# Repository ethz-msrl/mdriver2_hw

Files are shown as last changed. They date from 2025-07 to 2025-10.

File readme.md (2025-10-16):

# MDriver2 Hardware
This repository contains the hardware design files of the `MDriver2` project.
## Control Hardware
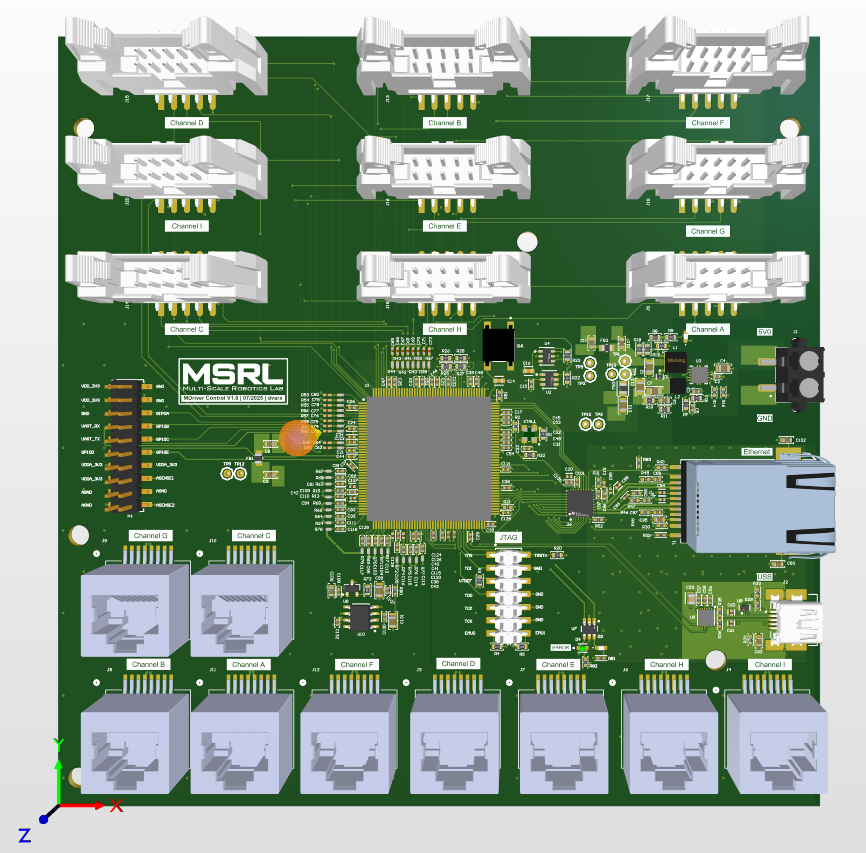
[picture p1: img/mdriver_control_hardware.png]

## Power Hardware
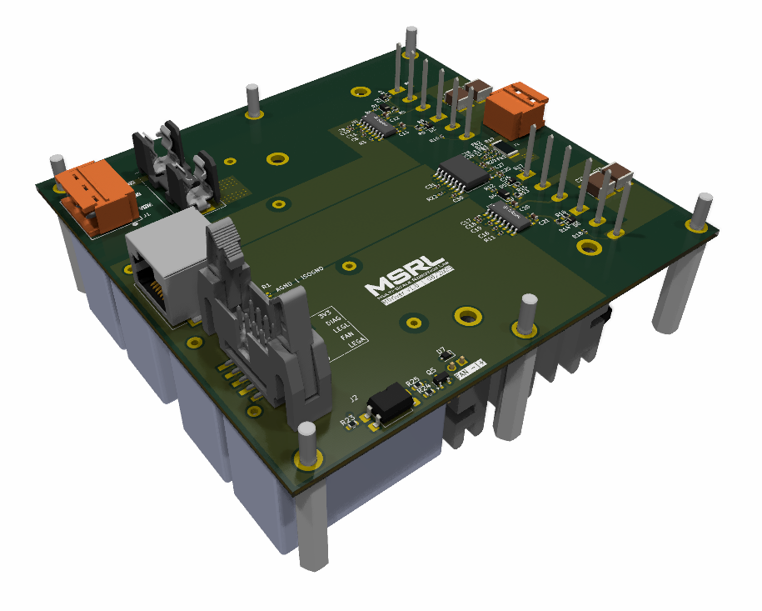
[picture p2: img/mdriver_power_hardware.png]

## Experimental Setup Overview
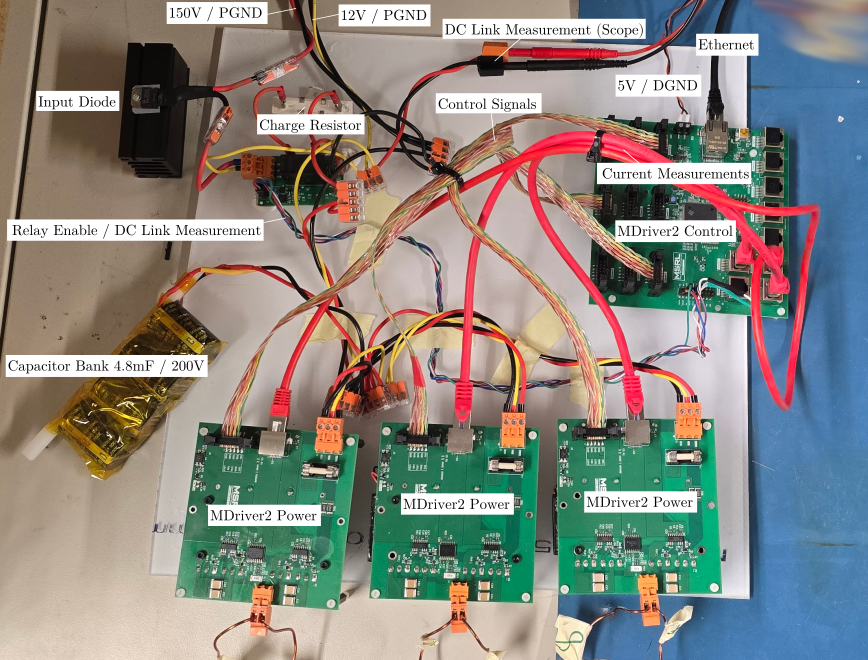
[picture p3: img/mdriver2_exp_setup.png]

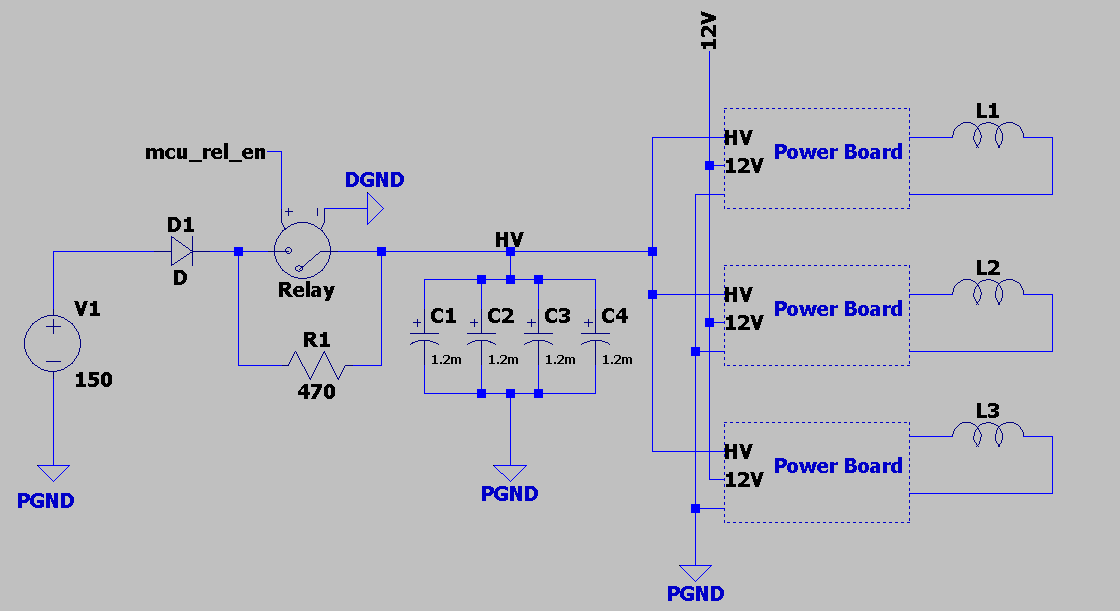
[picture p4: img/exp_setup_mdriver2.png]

- The input diode `D1` is optional and used to protect the supply `V1`.
- The charge resistor `R1` is used to limit excessive inrush current to the capcacitor bank but may not be needed for all supplies.
- The DC link voltage `VH` is monitored using an isolated DC measurement from the `capbank` PCB. Voltage values are transmitted via delta-sigma modulation to the microcontroller.

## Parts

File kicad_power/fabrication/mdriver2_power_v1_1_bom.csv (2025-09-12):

Reference | Qty | Partno | Description | Footprint
C6,C8,C11,C16,C19,C26,C27,C29,C30,C31,C32,C33 | 12 | C0402C104K4RECAUTO | Multilayer Ceramic Capacitors MLCC - SMD/SMT 16V 0.1uF X7R 0402 10% | Capacitor_SMD:C_0402_1005Metric
C7,C12,C13,C20,C21,C34 | 6 | CGA3E1X7S1C225K080AE | Cap Ceramic 2.2uF 16V X7S 10% Pad SMD 0603 Soft Termination 125C Automotive T/R | Capacitor_SMD:C_0603_1608Metric
C9,C10,C17,C18 | 4 | VJ0402A101JXACW1BC | 0402 100 pF 50 V ±5% Tolerance C0G/NP0 SMT Multilayer Ceramic Chip Capacitor | Capacitor_SMD:C_0402_1005Metric
C14,C15,C22,C23 | 4 | 885342214001 | Cap, 1Uf, 630V, Mlcc, 2220 Rohs Compliant: Yes |Wurth Elektronik 885342214001 | Capacitor_SMD:C_2220_5750Metric_Pad1.97x5.40mm_HandSolder
C24,C25 | 2 | 0402YD105KAT2A | Multilayer Ceramic Capacitor, 1uF, 10%, X5R, 16 V, 0402 [1005 Metric] Rohs Compliant: Yes | Capacitor_SMD:C_0402_1005Metric
C28 | 1 | CL05B102KB5NNNC | 1000 pF ±10% 50V Ceramic Capacitor X7R 0402 (1005 Metric) | Capacitor_SMD:C_0402_1005Metric
D1,D4 | 2 | ES1JFL | ES1JFL Series 600 V 1 A Surface Mount Ultrafast Rectifier - SOD-123F | Diode_SMD:D_SOD-123F
D2,D3,D5,D6,D7 | 5 | SD107WS-7-F | SD107WS Series 30 V 750 mA Schottky Barrier Diode Surface Mount - SOD-323 | Diode_SMD:D_SOD-323F
F1 | 1 | 0031.8225 | Fuse Block 10 A 500V 1 Circuit Cartridge Surface Mount | mdriver:fuse
FB1,FB2,FB3 | 3 | 74269244182 | Ferrite Beads, 0.21A, 1.8Kohm, 25% Rohs Compliant: Yes |Wurth Elektronik 74269244182 | Inductor_SMD:L_0402_1005Metric
J2 | 1 | 3010-10-003-13-00 | Generic connector, double row, 02x05, odd/even pin numbering scheme (row 1 odd numbers, row 2 even numbers), script generated (kicad-library-utils/schlib/autogen/connector/) | mdriver:10pin_data_connector
J3 | 1 | 634008149821 | Modular Jack WR-MJ, Tab Up, Shielded, Horizontal Entry, SMT, 8P8C | mdriver:J_Wurth_WR-MJ_634008149821
Q5 | 1 | Nexperia BC817-25,235 | Single Bipolar Transistor, NPN, 45 V, 500 mA, 345 mW, SOT-23 (TO-236AB), 3 Pins, Surface Mount | Package_TO_SOT_SMD:SOT-23
R2 | 1 | CRCW04021M00FKED | 63mW Thick Film Resistors 75V ±1% ±100ppm/℃ 1MΩ 0402 Chip Resistor - Surface Mount ROHS | Resistor_SMD:R_0402_1005Metric
R3,R11 | 2 | RCA04020000ZSED | Zero Ohm Resistor, Jumper, 0402 [1005 Metric], Thick Film, 63 mW, 1.5 A, Surface Mount Device | Resistor_SMD:R_0402_1005Metric
R4,R12 | 2 | CRGP1206F18R | Res Thick Film 1206 18 Ohm 1% 0.5W(1/2W) ±100ppm/C Pad SMD Automotive T/R | Resistor_SMD:R_1206_3216Metric
R5,R6,R13,R14 | 4 | CRCW06030000ZSTB | Zero Ohm Resistor, Jumper, 0603 [1608Metric], Thick Film, 100 mW, 2 A, Surface Mount | Resistor_SMD:R_0603_1608Metric
R7,R8,R15,R16 | 4 | ERJPA3F12R0V | Res Thick Film 0603 12 Ohm 1% 0.25W(1/4W) ±100ppm/C Pad SMD T/R Automotive AEC-Q200 | Resistor_SMD:R_0603_1608Metric
R9,R10,R17,R18 | 4 | CRGCQ0402F560K | Res Thick Film 0402 560K Ohm 1% 0.063W(1/16W) ±100ppm/C Pad SMD Automotive T/R | Resistor_SMD:R_0402_1005Metric
R19 | 1 | MCS3264R005FER | Fixed Resistor, 2W, 0.005ohm, 0.1V, 1% +/-Tol, 100ppm/Cel, Surface Mount, 2512 | Resistor_SMD:R_2512_6332Metric_Pad1.40x3.35mm_HandSolder
R20,R21 | 2 | RC0402JR-0710RL | Res Thick Film 0402 10 Ohm 5% 0.063W(1/16W) ±200ppm/C Pad SMD T/R | Resistor_SMD:R_0402_1005Metric
R22 | 1 | CRGP0402F47K | TE Connectivity CRGP0402F47K Res Thick Film 0402 47K Ohm 1% 0.125W(1/8W) ±100ppm/°C Pad SMD T/R Automotive AEC-Q200 | Resistor_SMD:R_0402_1005Metric
R23,R24,R25 | 3 | ERJ-PA3F4300V | Res Thick Film 0603 430 Ohm 1% 0.25W(1/4W) ±100ppm/C Pad SMD T/R Automotive AEC-Q200 | Resistor_SMD:R_0603_1608Metric
R26,R27 | 2 | 4-2176331-7 | Fixed Resistor, Thick Film, 2W, 68000ohm, 500V, 1% +/-Tol, 100ppm/Cel, Surface Mount, 2512 | Resistor_SMD:R_2512_6332Metric
U1,U2 | 2 | 2EDB8259YXUMA1 | Fast, robust, dual-channel, functional isolated MOSFET gate drivers with accurate and stable timing. | mdriver:SOIC-16
U3 | 1 | AMC3302DWER | ±50-mV input, precision current sensing reinforced isolated amplifier with integrated DC/DC | mdriver:AMC3302DWER
U4 | 1 | SFH617A-1X007T | Optocoupler, Phototransistor Output, 5300 VRMS, VCEO 70V, CTR% 40-80, -55 to +110 degree Celsius, UL, BSI, FIMKO, cUL, 8mm clearence SMD PDIP-4 | Package_DIP:SMDIP-4_W9.53mm_Clearance8mm

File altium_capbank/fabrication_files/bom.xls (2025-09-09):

Comment | Designator | Footprint | JLCPCB
C0603 15,000 pF C0G 30ppm/°C 20.00% 25 V | C1, C4 | FP-C0603C-CF-MFG | C1596
MLCC 1uF 0603 | C3, C5, C6 | CAPC1608X87X35LL15T15 | C5673
Single Output LDO, 100 mA, Fixed 5 V Output, 5.38 to 16 V Input, with Low IQ, 5-pin SOT-23 (DBV), -40 to 125 degC, Green (RoHS & no Sb/Br) | U2 | DBV0005A_M | C9837
Schottky Barrier Diode, 2-Pin SOD-323, Pb-Free, Tape and Reel | D1 | ONSC-SOD-323-2-477-02_V | C21107
Resistor | R3 | RES 0805_2012 | C17444
SMT Resistor | R4, R5, R6, R8, R9, R10, R11, R7 | RES 0603_1608 | C22961
SMT Resistor | R2 | RES 0603_1608 | C23193
Chip Multilayer Ceramic Capacitors for General Purpose, 0603, 2.2uF, X7R, 15%, 10%, 10V | C2 | FP-GRM188-0_1-e0_2_0_5-MFG | C43922
MOSFET N-CH 60V 1.6A SOT23 | Q1 | FP-SOT23-MFG | C211403
Optocoupler Phototransistor Output, 6 V, 50 mA, -55 to 100 degC, 4-Pin SOIC, RoHS, Tape and Reel | U1 | VISH-SOP-4_A_V | C335248
&plusmn;1-V input, precision voltage sensing reinforced isolated modulator 8-SOIC -40 to 125 | U3 | AMC1336 | C1852019
CONN HEADER SMD 6POS 2.54mm | J2 | FP-TMM-103-01-G-D-SM-MFG | C192301

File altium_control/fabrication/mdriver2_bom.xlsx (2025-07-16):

Designator | Quantity | Description | Manufacturer Partno
C1, C4, C7, C99, C131 | 5 | MLCC 22uF 0805 5V | GRM21BR60J226ME39L
C2, C3, C5, C15, C17, C21, C22, C23, C24, C25, C26, C29, C30, C31, C32, C33, C34, C36, C37, C38, C39, C40, C41, C42, C43, C44, C45, C46, C47, C48, C49, C52, C53, C54, C56, C57, C58, C81, C82, C87, C88, C89, C90, C91, C92, C93, C94, C95, C96, C100, C103, C104, C105, C107, C108, C109, C110, C111, C112, C113, C114, C115, C116, C117, C118, C119, C120, C121, C122, C123, C124, C125, C130, C132 | 80 | MLCC 100nF 0402 10V | C0402C104K8PACTU
C6 | 1 | MLCC 33pF 0603 10V C0G | 06035A330JAT2A
C8, C9, C10, C11, C106 | 5 | MLCC 2.2uF 0603 10V | GRM188R71A225KE15D
C12, C13 | 2 | MLCC 10uF 0805 10V | C0805C106K8PACTU
C14, C16 | 2 | CAP CER 10000PF 50V X7R 0603 | CC0603KRX7R9BB103
C19, C98 | 2 | CAP CER 10UF 10V X5R 0402 | CL05A106MP5NUNC
C20, C55, C84, C86, C126, C127, C128, C129 | 8 | CAP CER 1UF 10V X5R 0402 | C0402C105K8PACTU
C59 | 1 | CAP CER 4.7UF 10V X5R 0805 | C0805C475K8PACTU
C60, C61 | 2 | CAP CER 47PF 50V C0G/NP0 0402 | C0402C470J5GACTU
C62, C83, C85, C102 | 4 | MLCC 4.7nF 0603 10V | C0603C472J5RACTU
C63, C64, C65, C66, C67, C68, C69, C70, C71, C72, C73, C74, C75, C76, C77, C78, C79, C80 | 18 | MLCC 0402 100pF | GRM1555C1H101JA01D
C97, C101 | 2 | MLCC 10nF 0402 5V | CC0402KRX7R7BB103
D1 | 1 | CFSH05-20L TR PBFREE Rectifier Diode, Schottky, 1 Phase, 1 Element, 0.1A, 30V V(RRM) | CFSH05-20L TR PBFREE
D2, D3 | 2 | 150060GS55040 WL-SMCD SMT Mono-color Chip LED Diffused | 150060GS55040
D4 | 1 | LED RED 0603 SMD | VLMS1300-GS08
FB1, FB2 | 2 | 60 Ohms @ 100 MHz 1 Power, Signal Line Ferrite Bead 0805 (2012 Metric) 5A 20mOhm | MH2029-600Y
FB3 | 1 | Chip Ferrite Bead, 0805, 220Ω @ 100MHz, 0.045Ω, 25%, 2A | BLM21PG221SN1D
J1 | 1 | SMD Terminal Block 6A | 691709710302
J2 | 1 | USB Connector, 30 V, 1 A, 0 to 50 degC, 5-Pin SMD, RoHS, Tape and Reel | 56579-0576
J3, J4, J6, J7, J8, J9, J10, J11, J12 | 9 | No Description Available | 1433900000
J5, J13, J14, J15, J16, J17, J18, J19, J20 | 9 | Pin header male 2x5 2.54mm | 3010-10-003-13-00
L1 | 1 | WE-LQS SMD Power Inductor, L=2.2 µH | 74404042022
L2 | 1 | WE-LQS SMD Power Inductor, L=3.3 µH | 74404032033
P1 | 1 | 0.025" SQ Post Header, Surface Mount, Vertical, -55 to 125 degC, 2.54 mm Pitch, 14-Pin, Male, RoHS | TSM-107-01-L-DV
P4 | 1 | Pin header SMD 10x2 | 61032021121
R1, R6, R7, R73 | 4 | Resistor 0Ohm 0603 | RC0603JR-070RL
R2 | 1 | Resistor 10Ohm 0402 | ERJ-2RKF10R0X
R3 | 1 | Resistor 100Ohm 0402 | ERJ-2RKF1000X
R4, R5, R29 | 3 | Resistor 4.7kOhm 0402 | ERJ-2RKF4701X
R8 | 1 | Resistor 340kOhm 0603 | CPF0603B340KE1
R9 | 1 | Resistor 680Ohm 0603 | ERJ-3EKF6800V
R10 | 1 | Resistor 22kOhm 0603 | RC0603FR-0722KL
R11 | 1 | Resistor 205kOhm 0603 | CRCW0603205KFKEA
R12 | 1 | Resistor 2kOhm 0603 | ERJ-3EKF2001V
R13, R15, R17, R24, R63, R64, R65, R66, R67, R68, R69, R70, R71, R72, R74, R75, R76, R77, R78, R79 | 20 | Resistor 150Ohm 0402 | RC0402FR-07150RL
R14, R21, R33, R52 | 4 | Resistor 10kOhm 0402 | CRCW040210K0FKEDHP
R16 | 1 | Resistor 100kOhm 0402 | ERJ-2RKF1003X
R18 | 1 | Resistor 200kOhm 0603 | CRCW0603200KFKEA
R19 | 1 | Resistor 75kOhm 0603 | CRCW060375K0FKEA
R20, R22, R23, R25, R26, R32 | 6 | Resistor 2.2kOhm 0603 | RC0603FR-072K2L
R27, R28 | 2 | Resistor 56kOhm 0603 | CRCW060356K0FKEA
R30 | 1 | Resistor 2.49kOhm 0402 1% | CRCW04022K49FKED
R31 | 1 | Resistor 4.87kOhm 0402 1% | CRCW04024K87FKED
R34 | 1 | Resistor 1MOhm 0402 | CRGCQ0402F1M0
R35, R36 | 2 | Resistor 27Ohm 0402 | RC0402FR-0727RL
R37, R38, R39, R40, R41, R42, R43, R44, R45, R50, R53, R54, R55, R56, R57, R58, R61, R62 | 18 | Resistor 5.6Ohm 0402 | RC0402FR-075R6L
R46, R47, R48, R49 | 4 | Resistor 49.9Ohm 0402 | ERJ-2RKF49R9X
R51, R83 | 2 | Resistor 2.2kOhm 0402 | RC0402JR-072K2L
R59, R60 | 2 | Resistor 470Ohm 0603 | RC0603FR-07470RL
R80 | 1 | Resistor 2.2kOhm 0402 | BLM15AG102SN1D
R81, R82 | 2 | Resistor 1kOhm 0402 1% | CRCW04021K00FKED
SW1 | 1 | SWITCH TACTILE SPST-NO 0.05A 12V | PTS645SM43SMTR92LFS
T1 | 1 | 7498010210A Telecom and Datacom Connector, 8 Contact(s), Female, Right Angle, Surface Mount Terminal | 7498010210A
U1 | 1 | XF28388DPTPS | F28388DPTPS
U2 | 1 | IC SUPERVISOR 1 CHANNEL TSOT23-6 | TPS3702CX33DDCT
U3 | 1 | Buck Adjustable Regulator with 2.5 to 6 V Input and 0.6 to 6 V Output, -40 to 85 degC, 10-Pin SON (DRC), Green (RoHS & no Sb/Br) | TPS62420DRCR
U4 | 1 | IC SUPERVISOR 1 CHANNEL TSOT23-6 | TPS3702CX12DDCT
U5 | 1 | IC USB SERIAL BASIC UART 12DFN | FT234XD-R
U6 | 1 | IC INTERFACE SPECIALIZED 32VQFN | DP83822IRHBR
U7 | 1 | Dual Buffer/Driver with Open-Drain Output, DBV0006A, LARGE T&R | SN74LVC2G07DBVR
U8 | 1 | 20 ppm / degC Max, 100 uA Series Voltage Reference, -40 to 125 degC, 3-pin SOT-23 (DBZ), Green (RoHS & no Sb/Br) | REF3130AIDBZR
U9 | 1 | TVS DIODE 5.5V 6SON | TPD4S012DRYR
U10 | 1 | High-Speed, Single-Supply, Rail-to-Rail Operational Amplifier MicroAmplifier(TM) Series, 2.7 to 5.5 V, -40 to 85 degC, 8-pin SOIC (D8), Green (RoHS & no Sb/Br) | OPA350UA/2K5
XTAL1 | 1 | 25MHz Oscillator | ECS-2520S33-250-FN-TR

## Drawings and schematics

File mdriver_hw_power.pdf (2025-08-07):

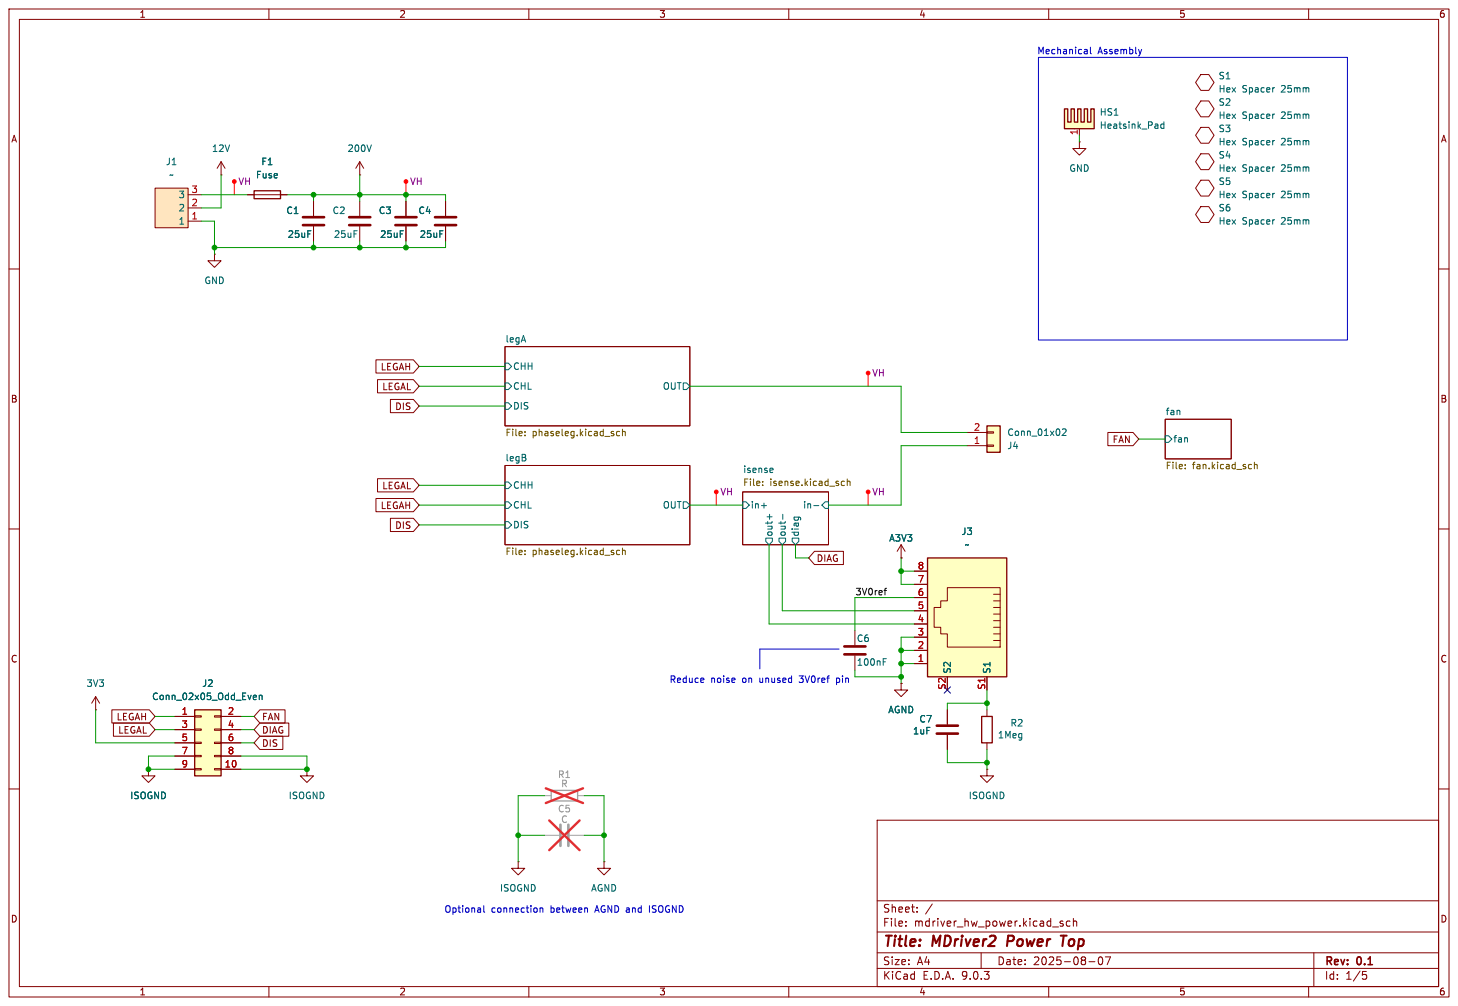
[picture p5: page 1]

fan File: fan.kicad_sch S6Hex Spacer 25mm

legB
isense File: isense.kicad_sch OUT CHH

File: mdriver_hw_power.kicad_sch Sheet: /
Id: 1/5 Title: MDriver2 Power Top

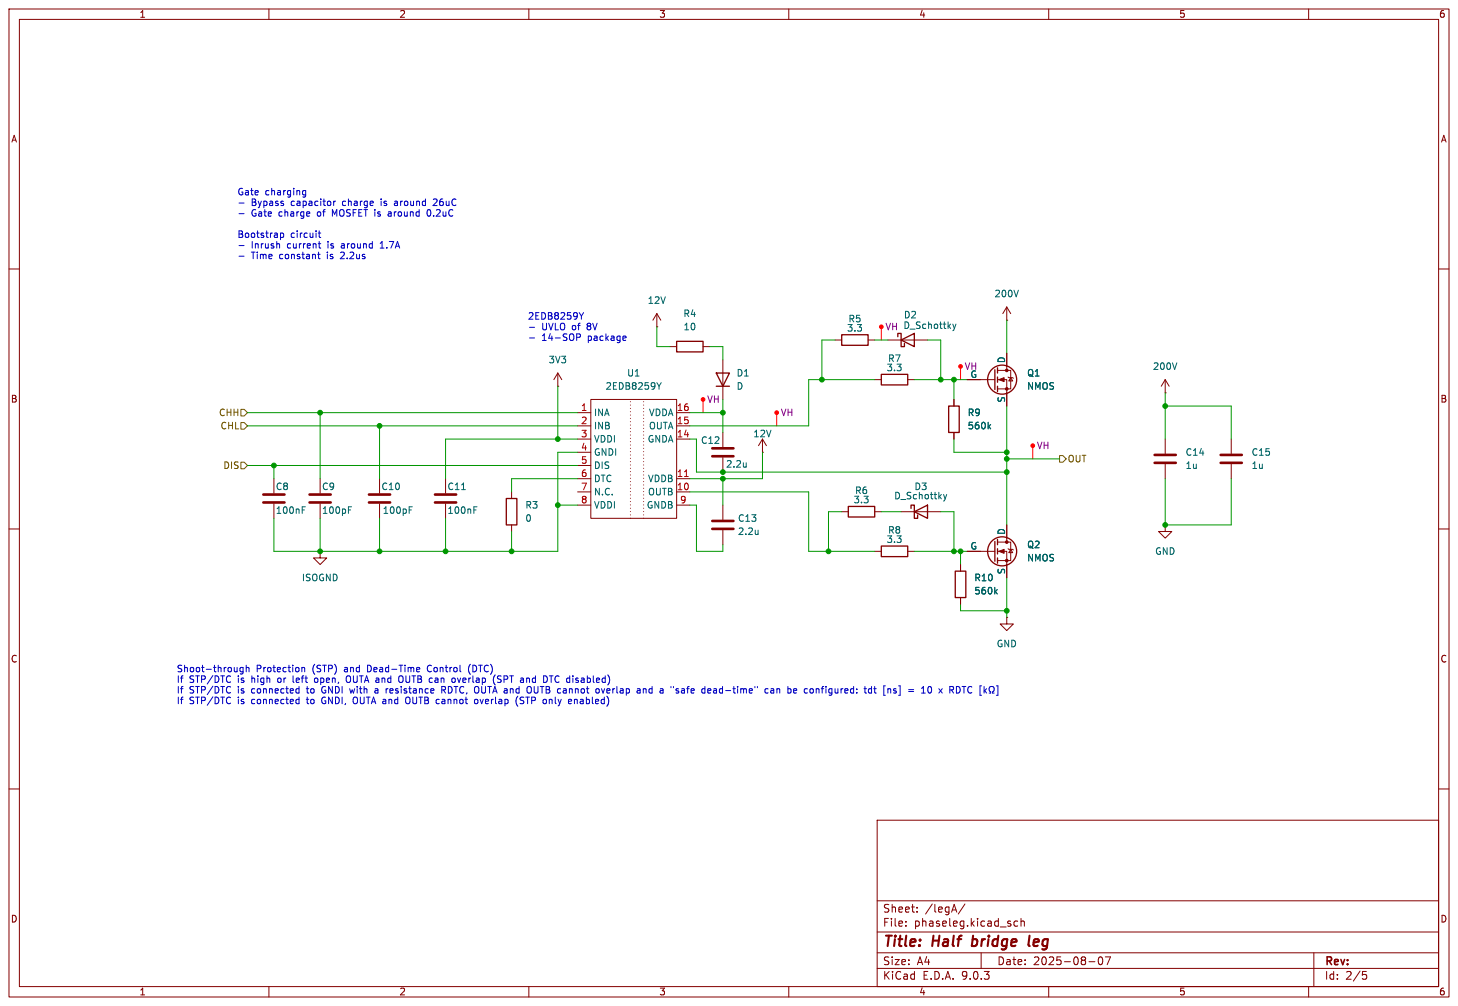
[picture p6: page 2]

- Gate charge of MOSFET is around 0.2uC

INB 2 VDDI 3 GNDI 4 DIS 5 DTC 6 N.C. 7 VDDI 8 INA 1 | VDDA 16 OUTA 15 GNDA 14 VDDB | 11 OUTB 10 GNDB 9 U1

If STP/DTC is high or left open, OUTA and OUTB can overlap (SPT and DTC disabled)

File: phaseleg.kicad_sch Sheet: /legA/
Id: 2/5 Title: Half bridge leg

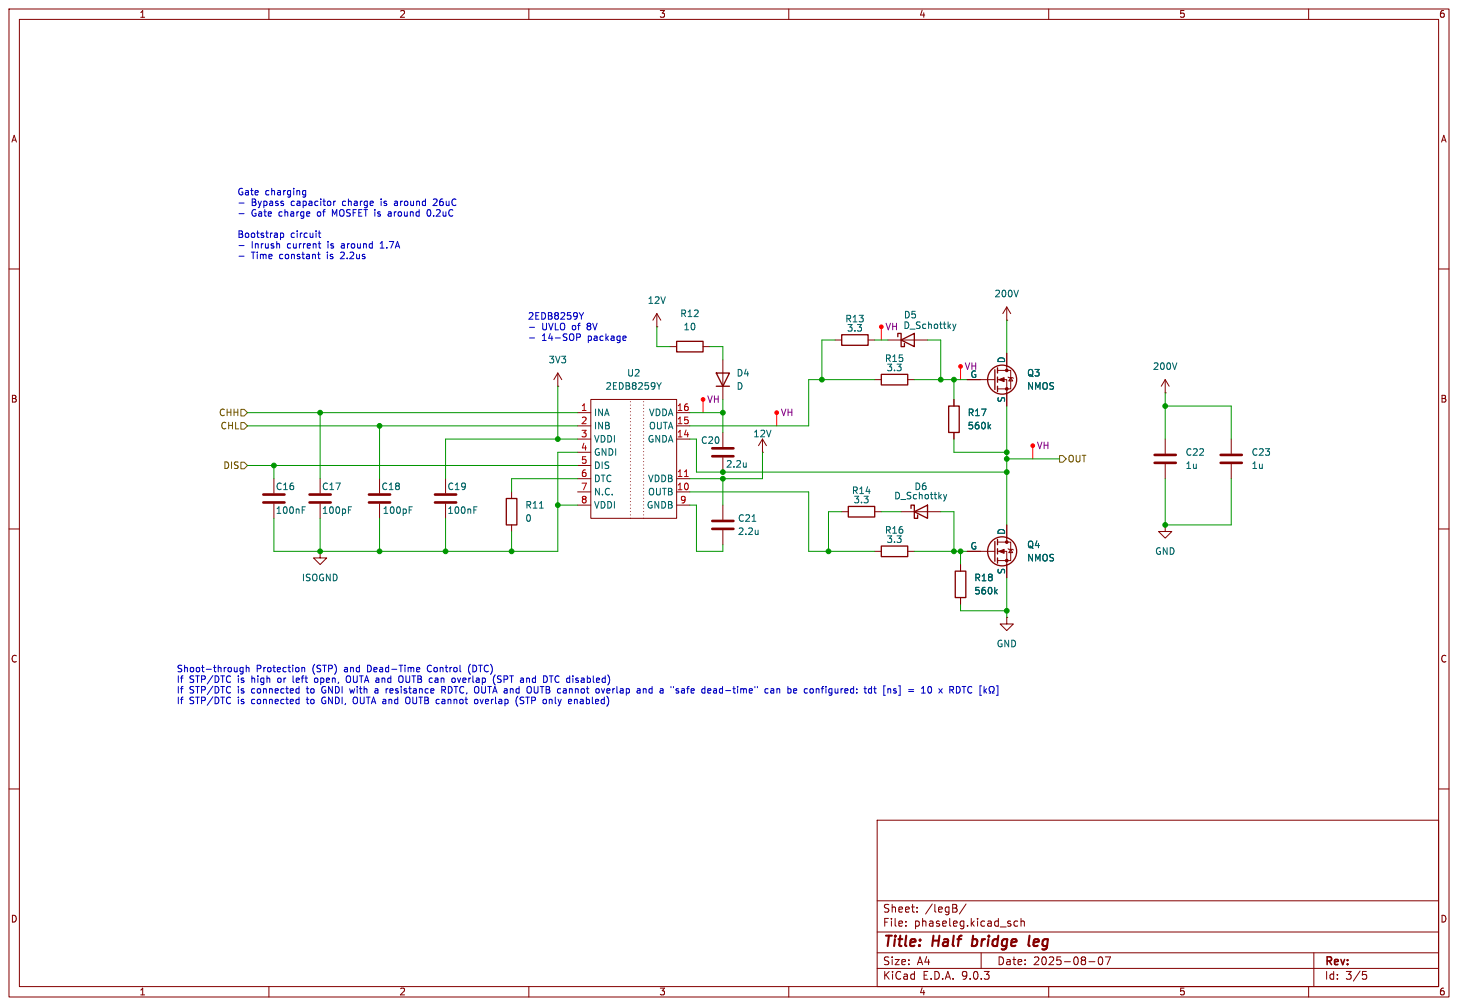
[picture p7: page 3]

- Gate charge of MOSFET is around 0.2uC

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

File: phaseleg.kicad_sch Sheet: /legB/
Id: 3/5 Title: Half bridge leg

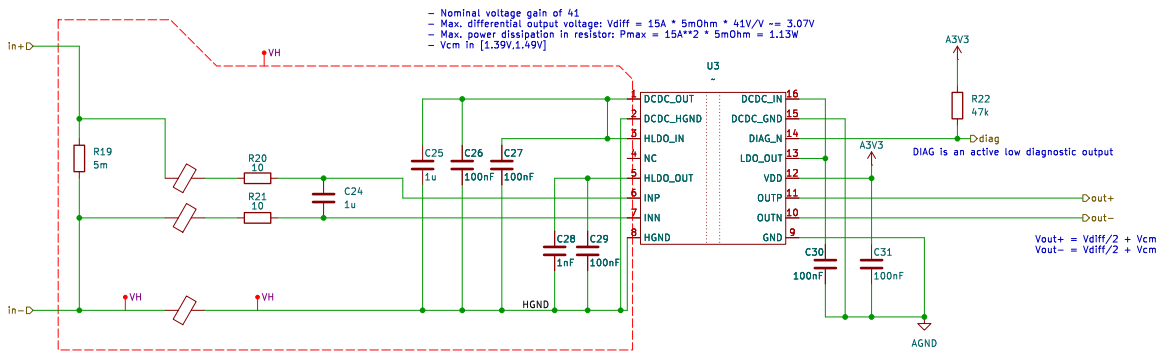
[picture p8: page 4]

- Nominal voltage gain of 41

File: isense.kicad_sch Sheet: /isense/
Id: 4/5 Title: Current sensing

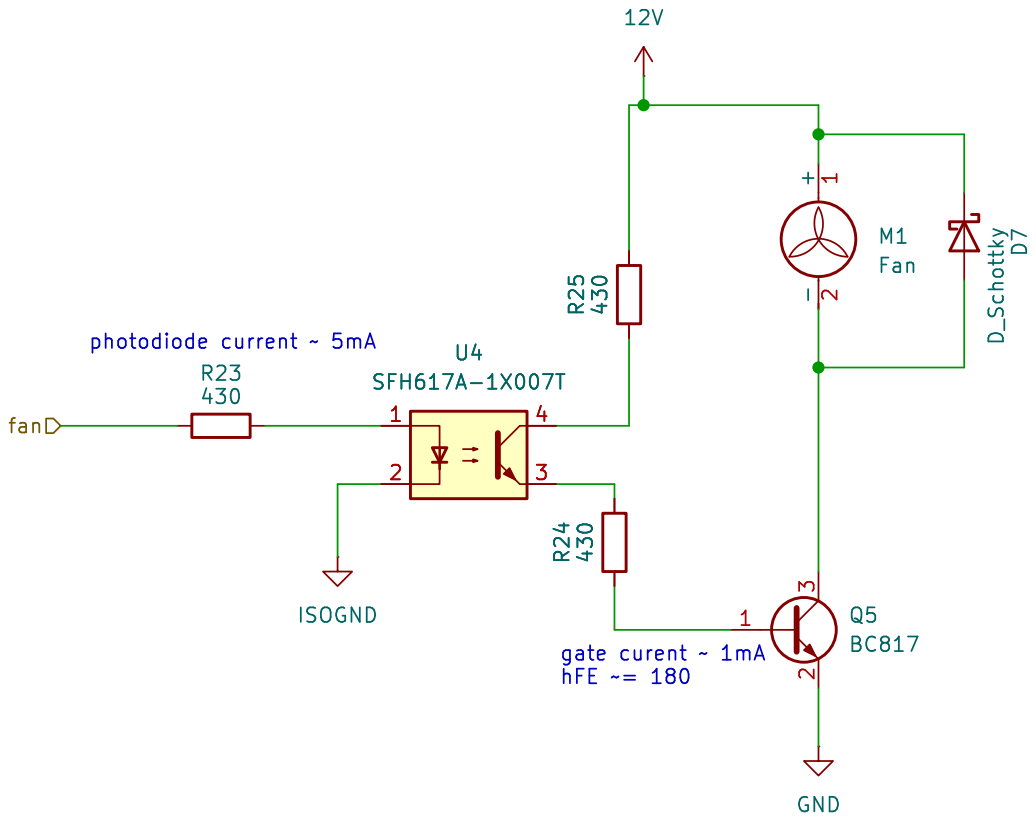
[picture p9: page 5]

Id: 5/5 Title: Cooling Fan Control File: fan.kicad_sch Sheet: /fan/ 1

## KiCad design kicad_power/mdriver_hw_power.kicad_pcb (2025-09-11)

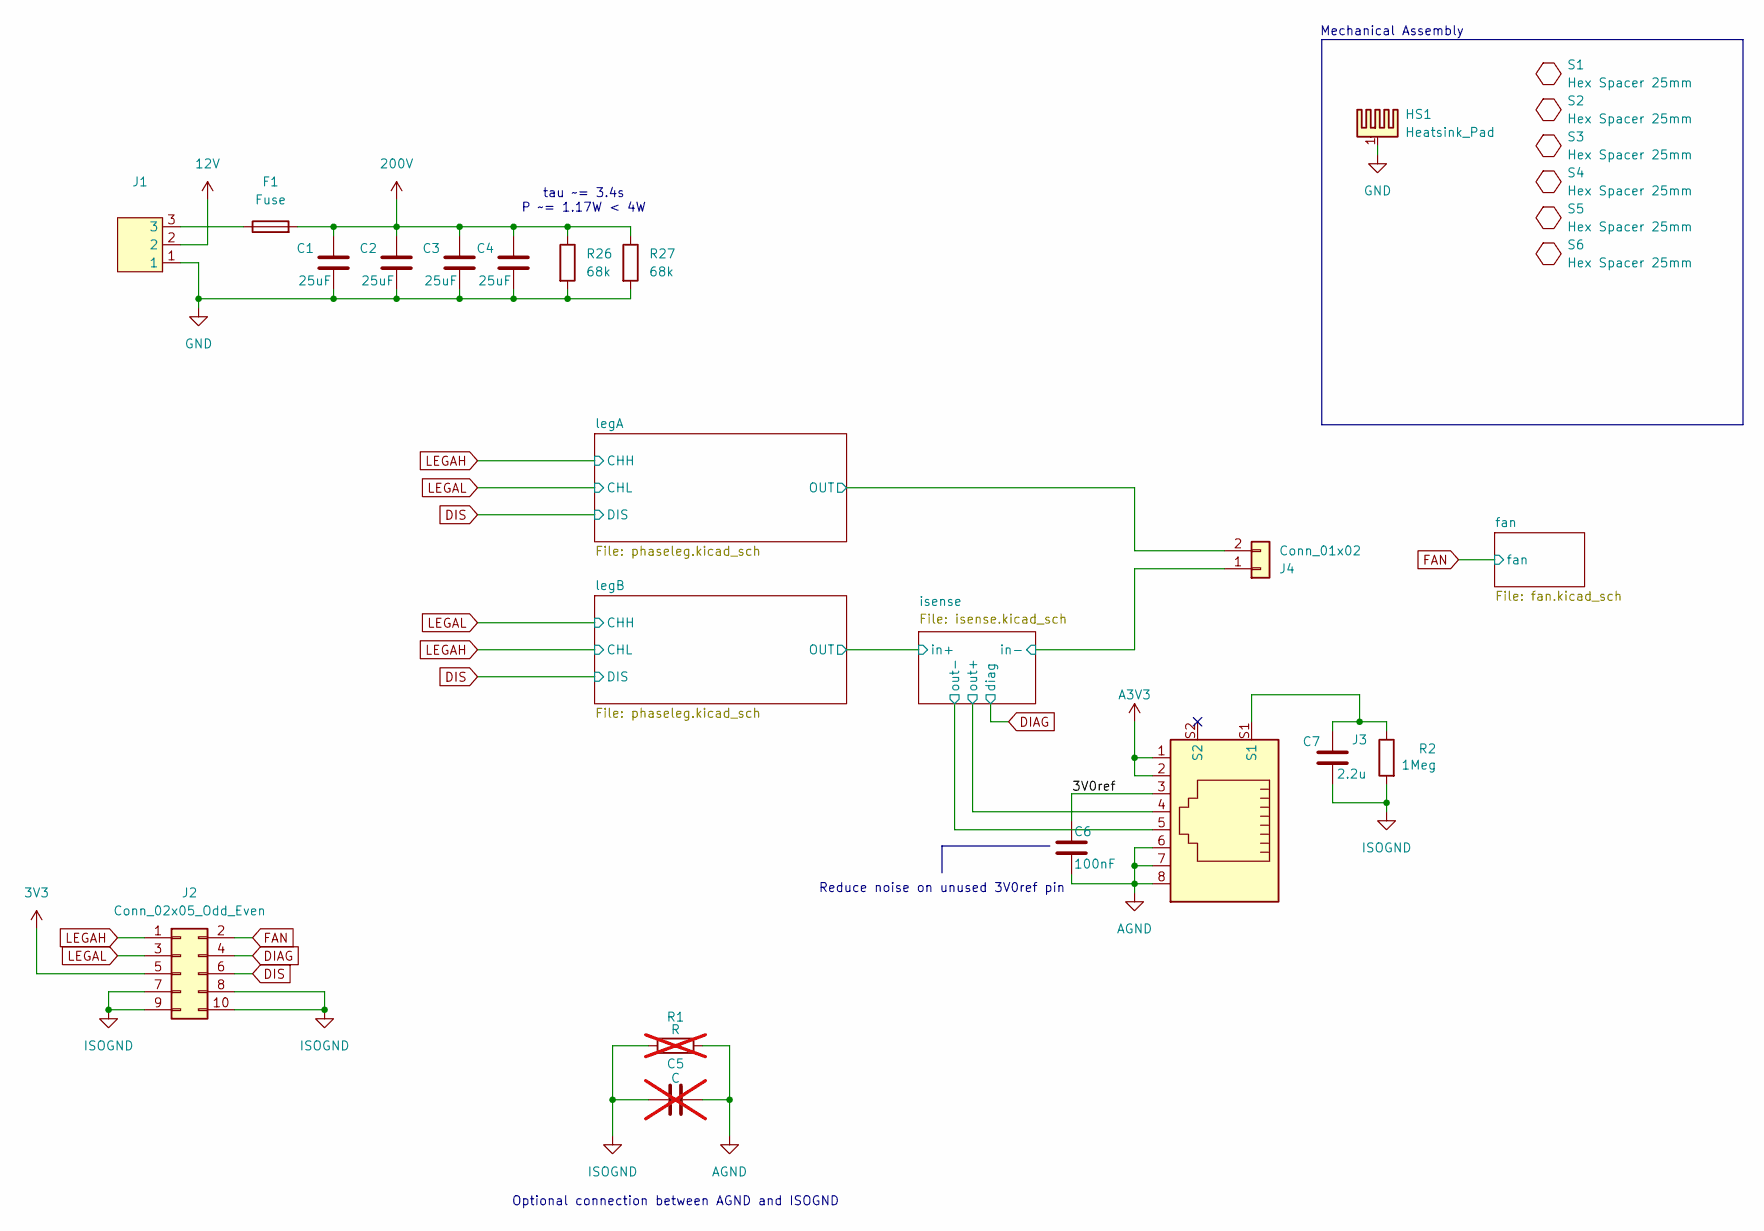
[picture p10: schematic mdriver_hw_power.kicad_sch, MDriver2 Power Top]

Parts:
C1, C2, C3, C4: 25uF; film_cap_25uF; Partno FB37F38I0256KC
C5: C; C_0402_1005Metric; not fitted
C6: 100nF; C_0402_1005Metric; Partno C0402C104K4RECAUTO; JLCPCB C1525
C7: 2.2u; C_0603_1608Metric; Partno CGA3E1X7S1C225K080AE; JLCPCB CL10A225KA8NNNC
F1: Fuse; fuse; Partno 0031.8225
HS1: Heatsink_Pad; heatsink_assman; Partno V5583K
J1: CONN_1148070000_WED; Partno 1148070000
J2: Conn_02x05_Odd_Even; 10pin_data_connector; Partno 3010-10-003-13-00
J3: J_Wurth_WR-MJ_634008149821; Partno 634008149821
J4: Conn_01x02; weidmuller_20A_2pin; Partno 1148030000
R1: R; R_0402_1005Metric; not fitted
R2: 1Meg; R_0402_1005Metric; Partno CRCW04021M00FKED; JLCPCB C26083
R26, R27: 68k; R_2512_6332Metric; Partno 4-2176331-7
S1, S2, S3, S4, S5, S6: Hex Spacer 25mm; hex_spacer; Partno 25506

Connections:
3V3: J2.5; also elsewhere on the board
12V: J1.2; also elsewhere on the board
200V: C1.1, C2.1, C3.1, C4.1, F1.2, R26.1, R27.1; also elsewhere on the board
/3V0ref: C6.1, J3.3
/isense/in-: J4.1; also elsewhere on the board
/isense/out+: J3.4; also elsewhere on the board
/isense/out-: J3.5; also elsewhere on the board
/legA/OUT: J4.2; also elsewhere on the board
A3V3: J3.1, J3.2; also elsewhere on the board
AGND: C5.2, C6.2, J3.6, J3.7, J3.8, R1.2; also elsewhere on the board
DIAG: J2.4; also elsewhere on the board
DIS: J2.6; also elsewhere on the board
FAN: J2.2; also elsewhere on the board
GND: C1.2, C2.2, C3.2, C4.2, HS1.1, J1.1, R26.2, R27.2; also elsewhere on the board
ISOGND: C5.1, C7.2, J2.7, J2.8, J2.9, J2.10, R1.1, R2.2; also elsewhere on the board
LEGAH: J2.1; also elsewhere on the board
LEGAL: J2.3; also elsewhere on the board
unnamed: C7.1, J3.S1, R2.1
unnamed: F1.1, J1.3

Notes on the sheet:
Optional connection between AGND and ISOGND
tau ~= 3.4s P ~= 1.17W < 4W
Mechanical Assembly
Reduce noise on unused 3V0ref pin

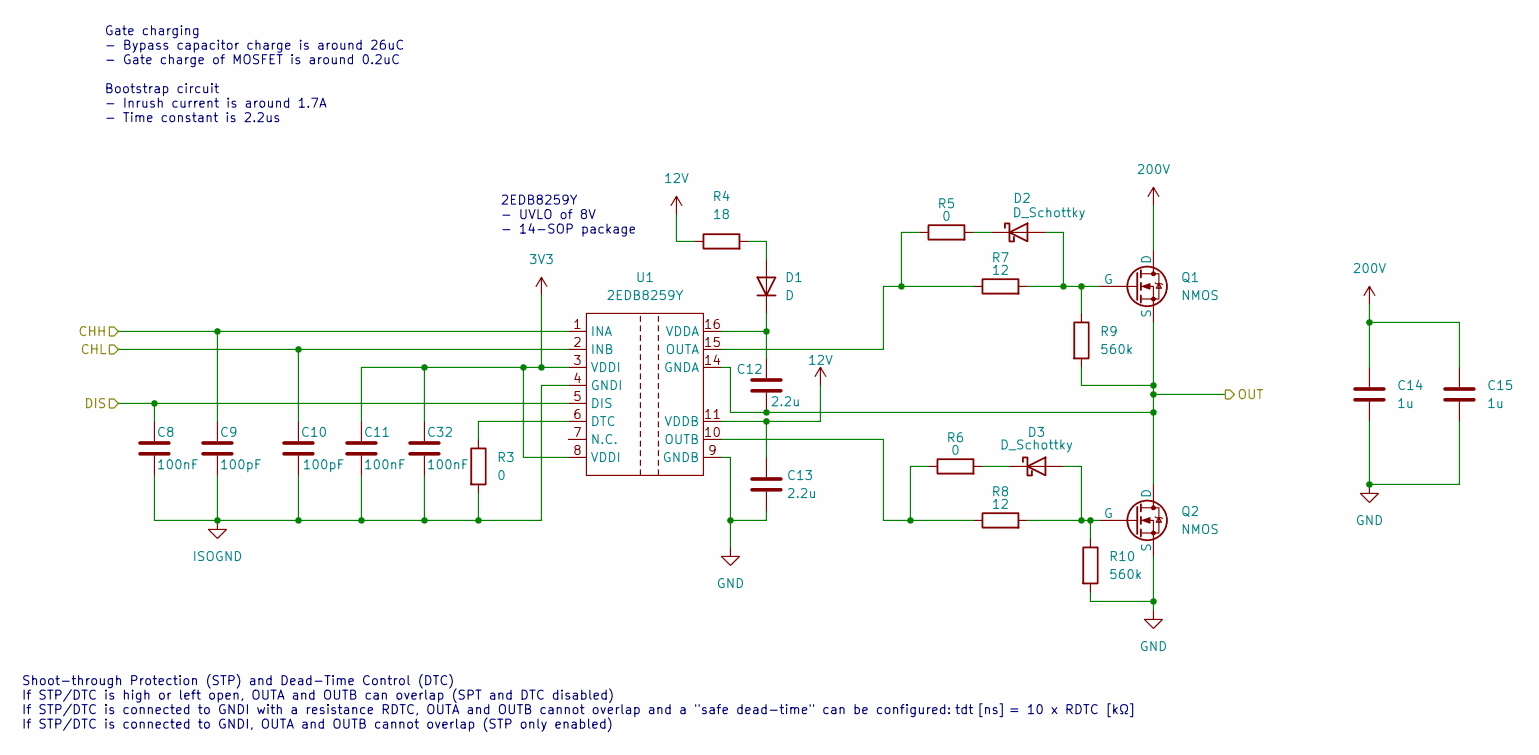
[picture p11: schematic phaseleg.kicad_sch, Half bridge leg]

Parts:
C8, C11, C32: 100nF; C_0402_1005Metric; Partno C0402C104K4RECAUTO; JLCPCB C1525
C9, C10: 100pF; C_0402_1005Metric; Partno VJ0402A101JXACW1BC; JLCPCB C26409
C12, C13: 2.2u; C_0603_1608Metric; Partno CGA3E1X7S1C225K080AE; JLCPCB CL10A225KA8NNNC
C14, C15: 1u; C_2220_5750Metric_Pad1.97x5.40mm_HandSolder; Partno 885342214001
D1: D; D_SOD-123F; Partno ES1JFL; JLCPCB C719809
D2, D3: D_Schottky; D_SOD-323F; Partno SD107WS-7-F; JLCPCB C124210
Q1, Q2: NMOS; TO-247-3_Vertical; Partno IPW60R024P7XKSA1
R3: 0; R_0402_1005Metric; Partno RCA04020000ZSED; JLCPCB C17168
R4: 18; R_1206_3216Metric; Partno CRGP1206F18R
R5, R6: 0; R_0603_1608Metric; Partno CRCW06030000ZSTB; JLCPCB C25165
R7, R8: 12; R_0603_1608Metric; Partno ERJPA3F12R0V
R9, R10: 560k; R_0402_1005Metric; Partno CRGCQ0402F560K; JLCPCB C15785
U1: 2EDB8259Y; SOIC-16; Partno 2EDB8259YXUMA1

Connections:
3V3: C11.1, C32.1, U1.3 (VDDI), U1.8 (VDDI); also elsewhere on the board
12V: C13.1, R4.1, U1.11 (VDDB); also elsewhere on the board
200V: C14.1, C15.1, Q1.2 (D); also elsewhere on the board
/legA/OUT: C12.2, Q1.3 (S), Q2.2 (D), R9.2, U1.14 (GNDA); also elsewhere on the board
DIS: C8.1, U1.5 (DIS); also elsewhere on the board
GND: C13.2, C14.2, C15.2, Q2.3 (S), R10.2, U1.9 (GNDB); also elsewhere on the board
ISOGND: C8.2, C9.2, C10.2, C11.2, C32.2, R3.2, U1.4 (GNDI); also elsewhere on the board
LEGAH: C9.1, U1.1 (INA); also elsewhere on the board
LEGAL: C10.1, U1.2 (INB); also elsewhere on the board
unnamed: D1.2 (A), R4.2
unnamed: C12.1, D1.1 (K), U1.16 (VDDA)
unnamed: D2.2 (A), Q1.1 (G), R7.2, R9.1
unnamed: D2.1 (K), R5.2
unnamed: D3.2 (A), Q2.1 (G), R8.2, R10.1
unnamed: D3.1 (K), R6.2
unnamed: R3.1, U1.6 (DTC)
unnamed: R5.1, R7.1, U1.15 (OUTA)
unnamed: R6.1, R8.1, U1.10 (OUTB)

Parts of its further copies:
C16, C19, C33: 100nF; C_0402_1005Metric; Partno C0402C104K4RECAUTO; JLCPCB C1525
C17, C18: 100pF; C_0402_1005Metric; Partno VJ0402A101JXACW1BC; JLCPCB C26409
C20, C21: 2.2u; C_0603_1608Metric; Partno CGA3E1X7S1C225K080AE; JLCPCB CL10A225KA8NNNC
C22, C23: 1u; C_2220_5750Metric_Pad1.97x5.40mm_HandSolder; Partno 885342214001
D4: D; D_SOD-123F; Partno ES1JFL; JLCPCB C719809
D5, D6: D_Schottky; D_SOD-323F; Partno SD107WS-7-F; JLCPCB C124210
Q3, Q4: NMOS; TO-247-3_Vertical; Partno IPW60R024P7XKSA1
R11: 0; R_0402_1005Metric; Partno RCA04020000ZSED; JLCPCB C17168
R12: 18; R_1206_3216Metric; Partno CRGP1206F18R
R13: 0; R_0603_1608Metric; Partno CRCW06030000ZSTB; JLCPCB C25165
R15: 12; R_0603_1608Metric; Partno ERJPA3F12R0V
R17, R18: 560k; R_0402_1005Metric; Partno CRGCQ0402F560K; JLCPCB C15785
U2: 2EDB8259Y; SOIC-16; Partno 2EDB8259YXUMA1

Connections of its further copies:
3V3: C19.1, C33.1, U2.3 (VDDI), U2.8 (VDDI); also elsewhere on the board
12V: C21.1, R12.1, U2.11 (VDDB); also elsewhere on the board
200V: C22.1, C23.1, Q3.2 (D); also elsewhere on the board
/isense/in+: C20.2, Q3.3 (S), Q4.2 (D), R17.2, U2.14 (GNDA); also elsewhere on the board
DIS: C16.1, U2.5 (DIS); also elsewhere on the board
GND: C21.2, C22.2, C23.2, Q4.3 (S), R18.2, U2.9 (GNDB); also elsewhere on the board
ISOGND: C16.2, C17.2, C18.2, C19.2, C33.2, R11.2, U2.4 (GNDI); also elsewhere on the board
LEGAH: C18.1, U2.2 (INB); also elsewhere on the board
LEGAL: C17.1, U2.1 (INA); also elsewhere on the board
unnamed: D4.2 (A), R12.2
unnamed: C20.1, D4.1 (K), U2.16 (VDDA)
unnamed: D5.2 (A), Q3.1 (G), R15.2, R17.1
unnamed: D5.1 (K), R13.2
unnamed 30: D6.2 (A), Q4.1 (G), R18.1; also elsewhere on the board
unnamed 31: D6.1 (K); also elsewhere on the board
unnamed: R11.1, U2.6 (DTC)
unnamed: R13.1, R15.1, U2.15 (OUTA)
unnamed 45: U2.10 (OUTB); also elsewhere on the board

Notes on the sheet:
2EDB8259Y - UVLO of 8V - 14-SOP package
Shoot-through Protection (STP) and Dead-Time Control (DTC) If STP/DTC is high or left open, OUTA and OUTB can overlap (SPT and DTC disabled) If STP/DTC is connected to GNDI with a resistance RDTC, OUTA and OUTB cannot overlap and a "safe dead-time" can be configured: tdt [ns] = 10 x RDTC [kΩ] If ST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
Gate charging - Bypass capacitor charge is around 26uC - Gate charge of MOSFET is around 0.2uC Bootstrap circuit - Inrush current is around 1.7A - Time constant is 2.2us

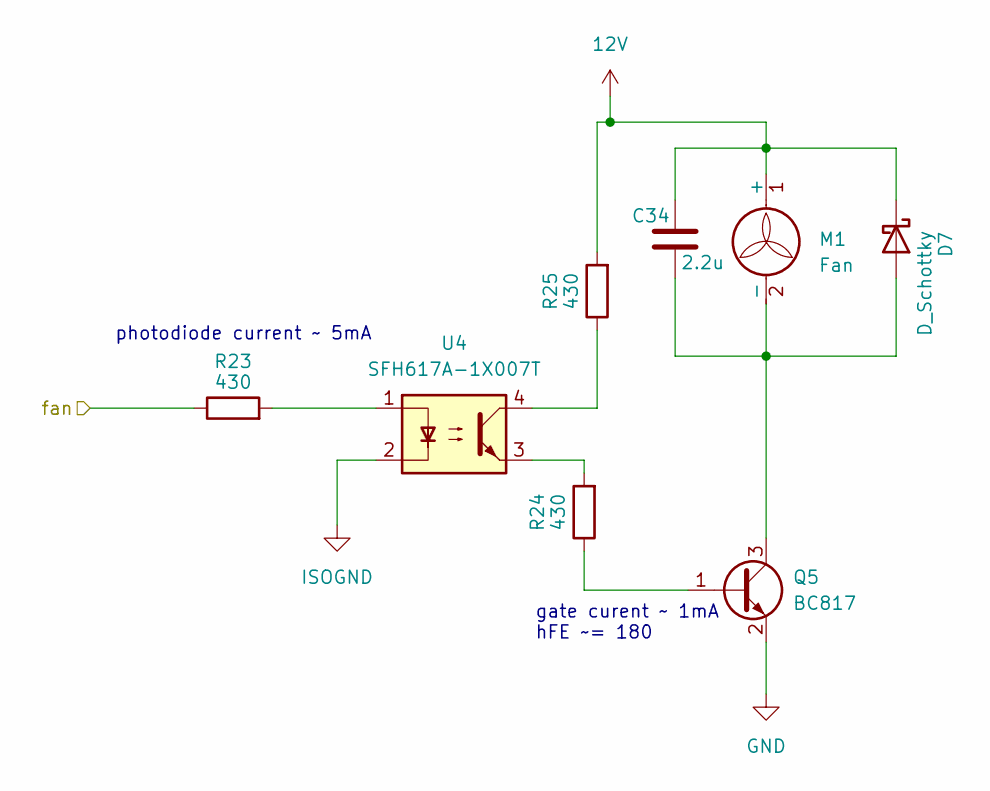
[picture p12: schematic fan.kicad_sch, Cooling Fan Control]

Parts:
C34: 2.2u; C_0603_1608Metric; Partno CGA3E1X7S1C225K080AE; JLCPCB CL10A225KA8NNNC
D7: D_Schottky; D_SOD-323F; Partno SD107WS-7-F; JLCPCB C124210
M1: Fan; PinHeader_1x02_P2.54mm_Vertical
Q5: BC817; SOT-23; Partno Nexperia BC817-25,235; JLCPCB C2137
R23, R24, R25: 430; R_0603_1608Metric; Partno ERJ-PA3F4300V; JLCPCB C23170
U4: SFH617A-1X007T; SMDIP-4_W9.53mm_Clearance8mm; Partno SFH617A-1X007T

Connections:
12V: C34.1, D7.1 (K), M1.1 (+), R25.2; also elsewhere on the board
FAN: R23.1; also elsewhere on the board
GND: Q5.2 (E); also elsewhere on the board
ISOGND: U4.2; also elsewhere on the board
unnamed: C34.2, D7.2 (A), M1.2 (-), Q5.3 (C)
unnamed: Q5.1 (B), R24.1
unnamed: R23.2, U4.1
unnamed: R24.2, U4.3
unnamed: R25.1, U4.4

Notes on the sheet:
gate curent ~ 1mA hFE ~= 180
photodiode current ~ 5mA

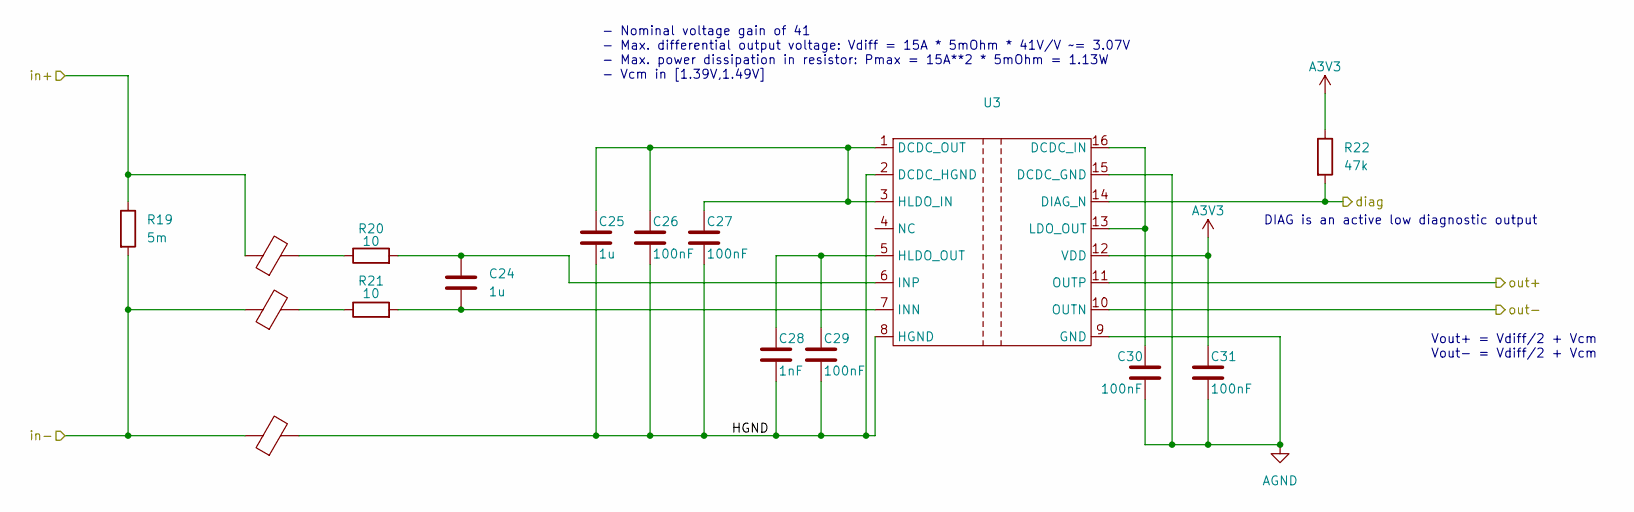
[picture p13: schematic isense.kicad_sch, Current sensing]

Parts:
C24, C25: 1u; C_0402_1005Metric; Partno 0402YD105KAT2A; JLCPCB C14445
C26, C27, C29, C30, C31: 100nF; C_0402_1005Metric; Partno C0402C104K4RECAUTO; JLCPCB C1525
C28: 1nF; C_0402_1005Metric; Partno CL05B102KB5NNNC; JLCPCB C1523
FB1, FB2, FB3: 2.2Ohm; L_0402_1005Metric; Partno 74269244182; JLCPCB C7038862
R19: 5m; R_2512_6332Metric_Pad1.40x3.35mm_HandSolder; Partno MCS3264R005FER; JLCPCB C108931
R20, R21: 10; R_0402_1005Metric; Partno RC0402JR-0710RL; JLCPCB C4109
R22: 47k; R_0402_1005Metric; Partno CRGP0402F47K; JLCPCB C25563
U3: AMC3302DWER; Partno AMC3302DWER; JLCPCB C4990160

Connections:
/isense/HGND: C25.2, C26.2, C27.2, C28.2, C29.2, FB3.2, U3.2 (DCDC_HGND), U3.8 (HGND)
/isense/in+: FB1.1, R19.1; also elsewhere on the board
/isense/in-: FB2.1, FB3.1, R19.2; also elsewhere on the board
/isense/out+: U3.11 (OUTP); also elsewhere on the board
/isense/out-: U3.10 (OUTN); also elsewhere on the board
A3V3: C31.1, R22.1, U3.12 (VDD); also elsewhere on the board
AGND: C30.2, C31.2, U3.9 (GND), U3.15 (DCDC_GND); also elsewhere on the board
DIAG: R22.2, U3.14 (DIAG_N); also elsewhere on the board
unnamed: FB1.2, R20.1
unnamed: FB2.2, R21.1
unnamed: C30.1, U3.13 (LDO_OUT), U3.16 (DCDC_IN)
unnamed: C25.1, C26.1, C27.1, U3.1 (DCDC_OUT), U3.3 (HLDO_IN)
unnamed: C28.1, C29.1, U3.5 (HLDO_OUT)
unnamed: C24.2, R21.2, U3.7 (INN)
unnamed: C24.1, R20.2, U3.6 (INP)

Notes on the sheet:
DIAG is an active low diagnostic output
Vout+ = Vdiff/2 + Vcm Vout- = Vdiff/2 + Vcm
- Nominal voltage gain of 41 - Max. differential output voltage: Vdiff = 15A * 5mOhm * 41V/V ~= 3.07V - Max. power dissipation in resistor: Pmax = 15A**2 * 5mOhm = 1.13W - Vcm in [1.39V,1.49V]

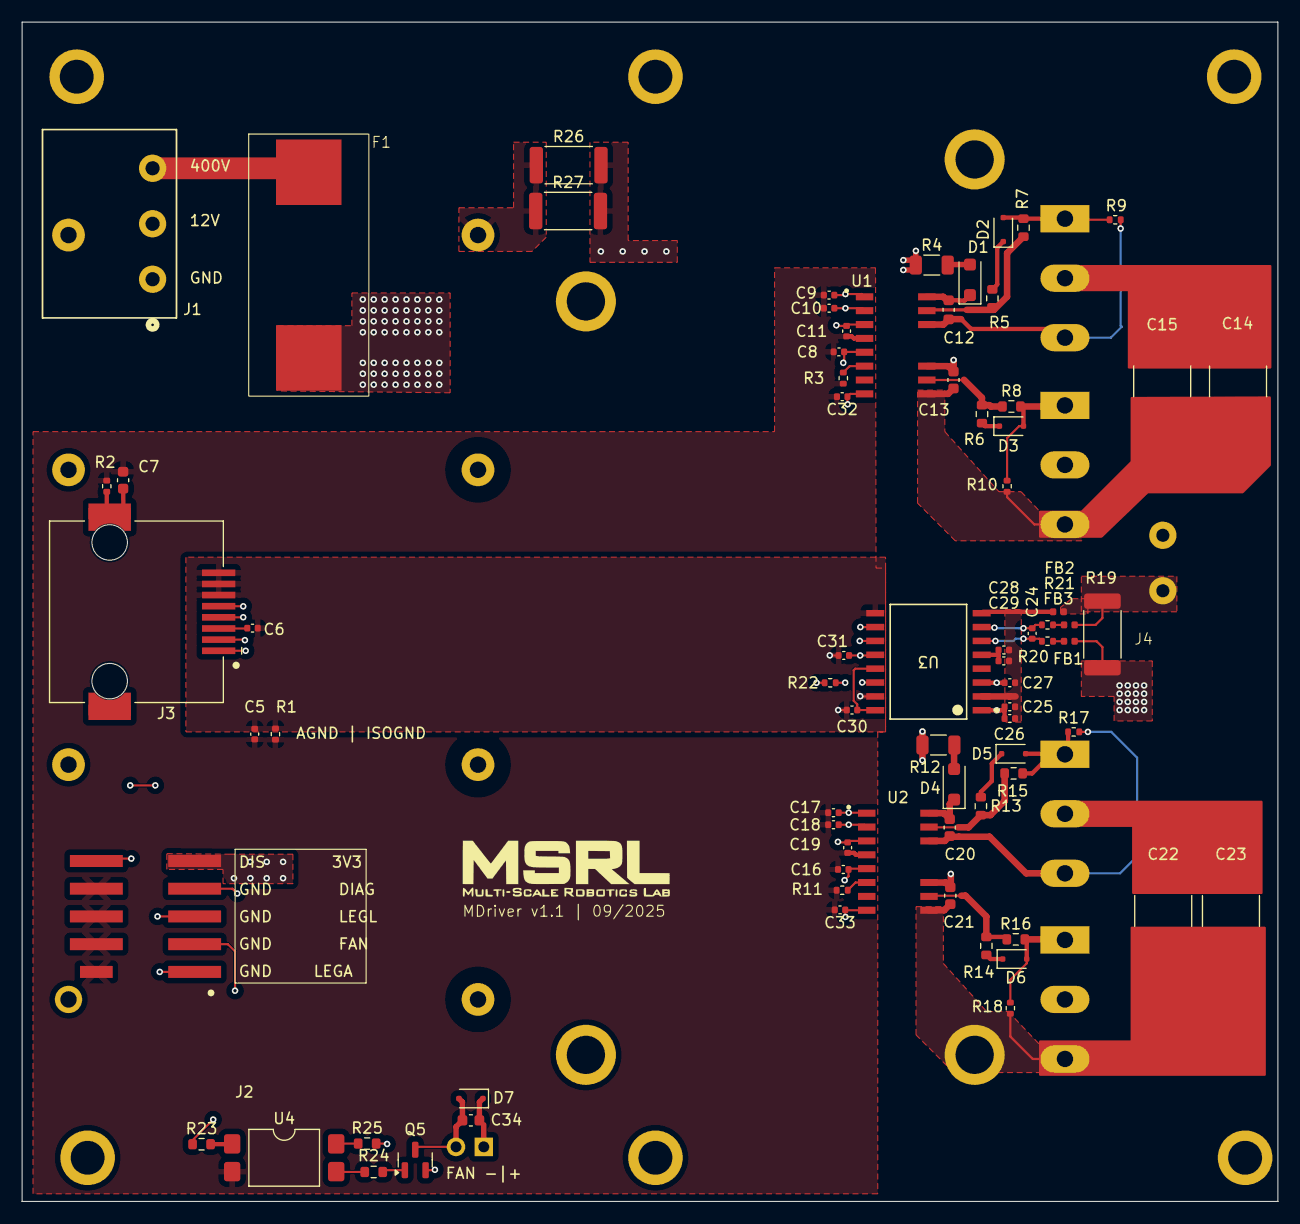
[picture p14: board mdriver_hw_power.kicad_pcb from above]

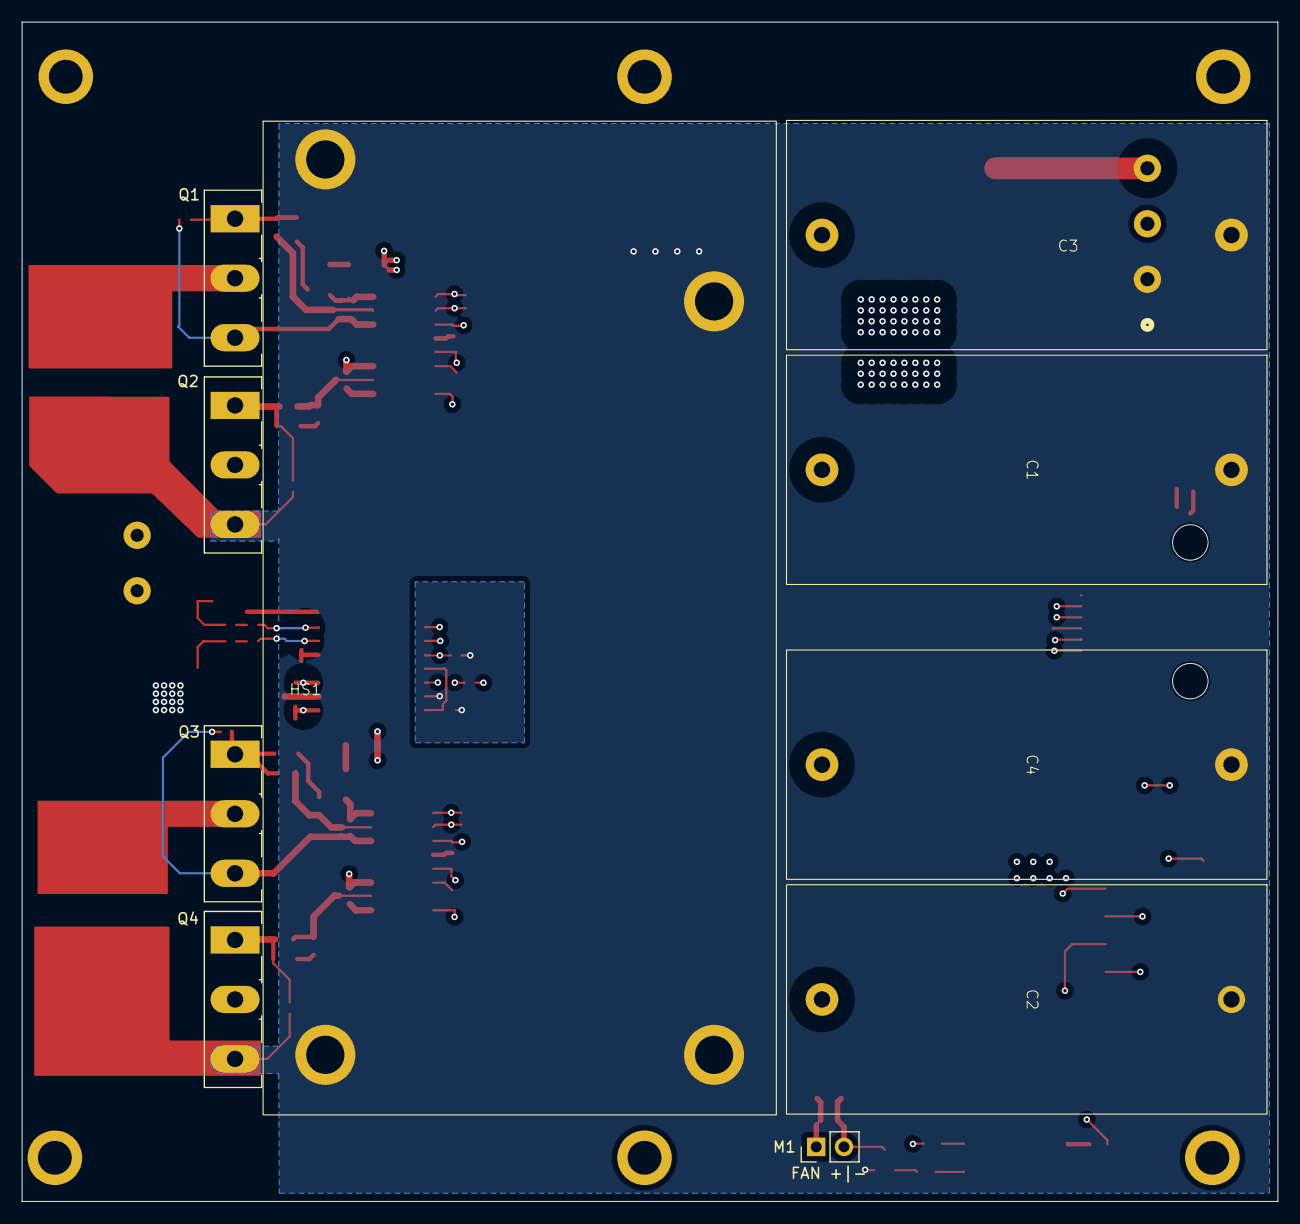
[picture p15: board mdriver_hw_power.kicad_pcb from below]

Board: 4 copper layers, 115.0 x 108.0 mm, 93 parts (16 on the bottom side), 51 nets.

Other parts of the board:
R14, R16: 3.3; R_0603_1608Metric

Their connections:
unnamed 30: R16.2; also elsewhere on the board
unnamed 31: R14.2; also elsewhere on the board
unnamed 45: R14.1, R16.1; also elsewhere on the board

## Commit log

2025-05-19 continue implementation of Ethernet interface
    [analog.SchDoc, ethernet.SchDoc, mcu.SchDoc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]
2025-05-25 completed schematic of Ethernet Section
    [ethernet.SchDoc, mcu.SchDoc]
2025-05-25 added usb/uart interface
    [analog.SchDoc, auxiliary.SchDoc, ethernet.SchDoc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]
2025-06-29 implemented layout of digital part
    [analog.SchDoc, auxiliary.SchDoc, ethernet.SchDoc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]
2025-06-30 finish initial implementation of digital layout
    [analog.SchDoc, ethernet.SchDoc, mcu.SchDoc]
2025-06-30 added layout file, completed layout of ADC channels
    [analog.SchDoc]
2025-07-01 finished initial layout wo all design rules
    [analog.SchDoc]
2025-07-01 changed layout to comply with pcbway design rules
    [analog.SchDoc]
2025-07-01 finished initial version of layout
    [auxiliary.SchDoc, mdriver2_control.PrjPcb]
2025-07-01 added missing supplier partno, increased distance between IDC headers
    [mcu.SchDoc]
2025-07-02 fixed various issues in schematics and updated layout, added datasheets
    [analog.SchDoc, auxiliary.SchDoc, ethernet.SchDoc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]
2025-07-02 added schematic and footprint library
    [analog.SchDoc, auxiliary.SchDoc, ethernet.SchDoc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]
2025-07-03 generated fabrication files
    [analog.SchDoc, auxiliary.SchDoc, ethernet.SchDoc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]
2025-07-03 adjusted BOM file
2025-07-04 fixed some issues with part description and adjusted BOM
    [auxiliary.SchDoc, ethernet.SchDoc, mcu.SchDoc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]
2025-07-07 added and changed folder structure
    [analog.SchDoc, auxiliary.SchDoc, ethernet.SchDoc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]
2025-07-16 removed unused MLCCs from schematic and BOM
    [mdriver2_bom.xlsx, power.SchDoc]
2025-07-16 fixed issue in parts description, footprint of RJ45 receptables, issues in BOM
    [analog.SchDoc, mdriver2_bom.xlsx, mdriver2_control.PcbLib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]
2025-07-28 restructured repo and added dimensioning scripts and project for power stage part
    [analog.SchDoc, auxiliary.SchDoc, bridge_leg.SchDoc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]
2025-07-29 added LTSpice simulation files for ripple simulations
    [bridge_leg.SchDoc]
2025-07-31 - Added current sensing - Finished initial version of layout - Added LTSpice simulation files
    [bridge_leg.SchDoc, current_sense.SchDoc, mdriver2_power_hw.PrjPcb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]
2025-08-01 added missing layout file
    [power.PcbDoc]
2025-08-04 added kicad power pcb project
    [fan.kicad_sch, isense.kicad_sch, mdriver_hw_power.kicad_pcb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]
2025-08-05 finished initial layout of power stage in KiCAD
    [fan.kicad_sch, isense.kicad_sch, mdriver2_power_hw.PrjPcb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]
2025-08-05 added step files and doc file
    [mdriver_hw_power.kicad_pcb]
2025-08-05 adjustment to PCB layout, created BOM file, added MOSFET gate discharge diodes
    [fan.kicad_sch, mdriver_hw_power.csv, mdriver_hw_power.kicad_pcb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]
2025-08-06 introduced AGND and A3V3, ensures HV design rules
    [fan.kicad_sch, isense.kicad_sch, mdriver_hw_power.csv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]
2025-08-07 finished initial version of power PCB
    [fan.kicad_sch, isense.kicad_sch, mdriver2_power_bom.csv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]
2025-08-22 corrected partname of AMC3302DWER
    [isense.kicad_sch, mdriver2_power_bom.csv, mdriver_hw_power.csv]
2025-09-09 added capbank pcb
    [auxiliary.SchDoc, bom.xls, capbank.PcbDoc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]
2025-09-09 adjusted footprint of SMD header
    [bom.xls, capbank.PcbDoc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]
2025-09-11 finished version 1.1 of power board
    [fan.kicad_sch, isense.kicad_sch, mdriver2_power_v1_1_bom.csv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]
2025-09-12 changed description of capacitor
    [isense.kicad_sch, mdriver2_power_v1_1_bom.csv]
2025-10-29 replaced bootstrap resistor with anti-surge resistor
    [phaseleg.kicad_sch]
